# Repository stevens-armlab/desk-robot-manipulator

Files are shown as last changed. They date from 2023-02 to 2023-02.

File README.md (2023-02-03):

# desk-robot-manipulator

## Open-Source Desk Robot Manipulator Design Project
This project is designed to cater towards the growing demand of more ubiquitous open-source robotics software and hardware. The files below provide the materials and resources necessary to recreate this desktop serial robot manipulator with a parallel gripper. 

## CAD Files
Included are individual SolidWorks CAD part files and an overall CAD assembly to help for 3D printing and assembling.
* Download documents as *.stl* files to print on any 3D printer
* This robot uses 5 Dynamixel XL430-W250-T servo motors which can be found [here](https://www.robotis.us/dynamixel-xl430-w250-t/)
* Screws can be found through these links below:
  * [6 - 16mm M2.5](https://www.mcmaster.com/screws/system-of-measurement~metric/thread-size~m2-5/metric-alloy-steel-hex-drive-flat-head-screws/length~16-mm/)
  * [4 - 10mm M2.5](https://www.mcmaster.com/screws/system-of-measurement~metric/thread-size~m2-5/metric-alloy-steel-hex-drive-flat-head-screws/length~10-mm/)
  * [8 - 12mm M2.5](https://www.mcmaster.com/screws/system-of-measurement~metric/thread-size~m2-5/metric-alloy-steel-hex-drive-flat-head-screws/length~12-mm/)
  * [12 - 8mm M2](https://www.mcmaster.com/screws/system-of-measurement~metric/metric-alloy-steel-hex-drive-flat-head-screws/thread-size~m2/length~8-mm)

## Arduino Program
This desk robot uses an [Arduino MEGA](https://store-usa.arduino.cc/products/arduino-mega-2560-rev3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), [Dynamixel Motor Shield](https://www.robotis.us/dynamixel-shield/), [SparkFun Serial Basic Communications Chip](https://www.sparkfun.com/products/14050), and the Arduino IDE as the robot's control mechanisms. To make edits to the code and test out additional programs install [Arduino IDE](https://support.arduino.cc/hc/en-us/articles/360019833020-Download-and-install-Arduino-IDE) and download the DynamixelShield Arduino library [here](https://github.com/ROBOTIS-GIT/DynamixelShield). These will allow you to program using Dynamixel software and upload code to the manipulator. 

Included in this package is the *move_all_motors.ino* Arduino program which takes in input keys *a, w, s, d, j, i, k, l* to control the position of each individual Dynamixel servo. T

Specifications:
* XL430 Dynamixel Servo Motor can be found [here](https://emanual.robotis.com/docs/en/dxl/x/xl430-w250/)
* Dynamixel Motor Shield can be found [here](https://emanual.robotis.com/docs/en/parts/interface/dynamixel_shield/)

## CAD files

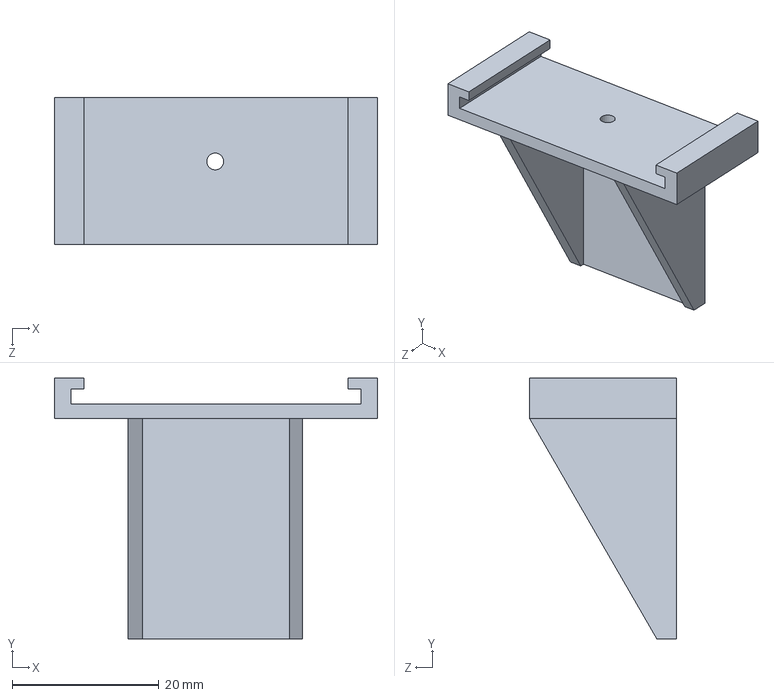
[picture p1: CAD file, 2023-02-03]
CAD Models/robothon_parallelgripper_hand_v4_other_side.SLDPRT
44.0 x 35.5 x 20.0 mm

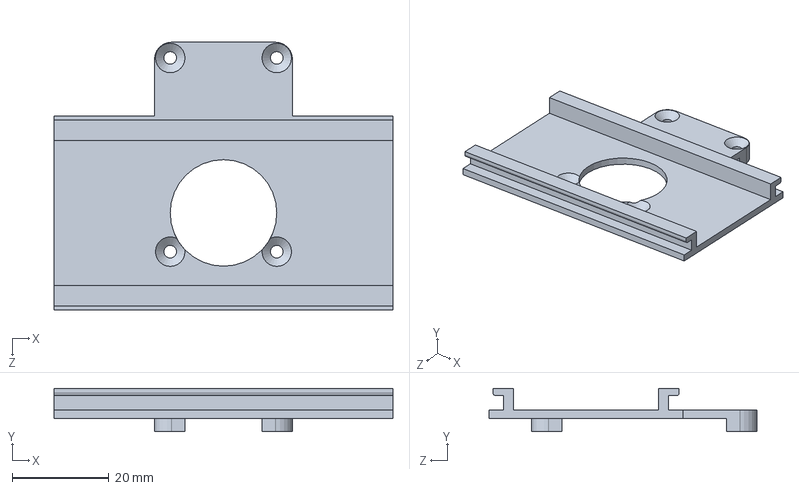
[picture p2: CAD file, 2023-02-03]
CAD Models/robothon_parallelgripper_plate_v4.SLDPRT
70.0 x 8.95 x 55.2 mm

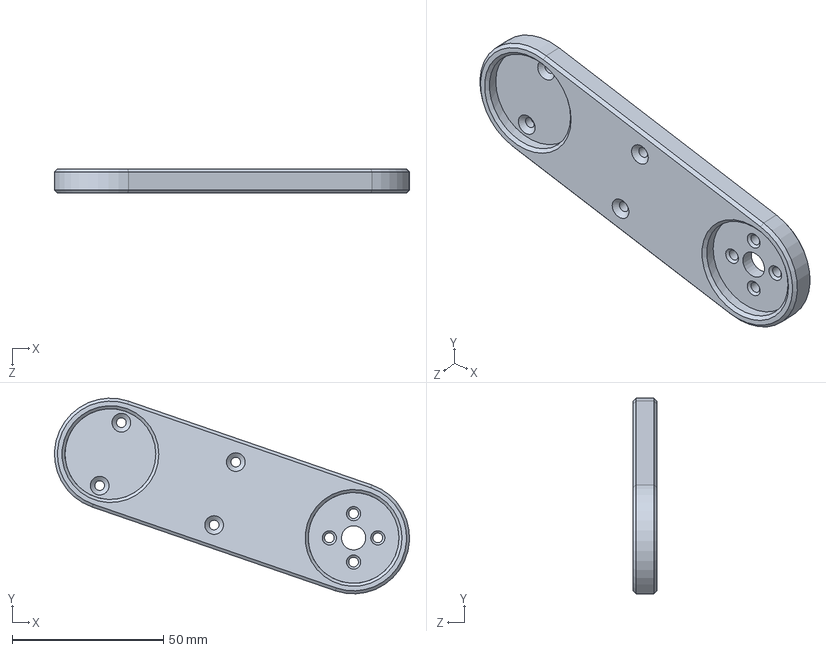
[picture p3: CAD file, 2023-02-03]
CAD Models/Joint 2.SLDPRT
117.3 x 64.7 x 8.00 mm

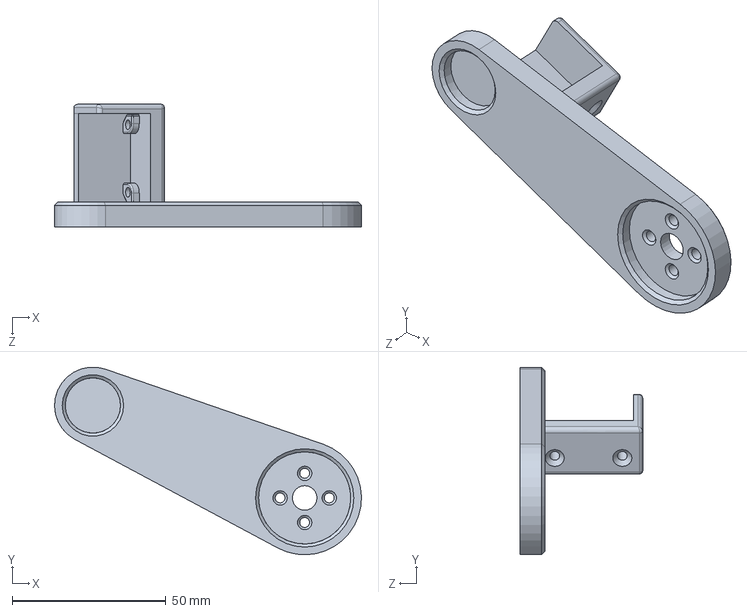
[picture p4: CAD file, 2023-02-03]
CAD Models/Joint 3.SLDPRT
100.0 x 61.0 x 39.9 mm

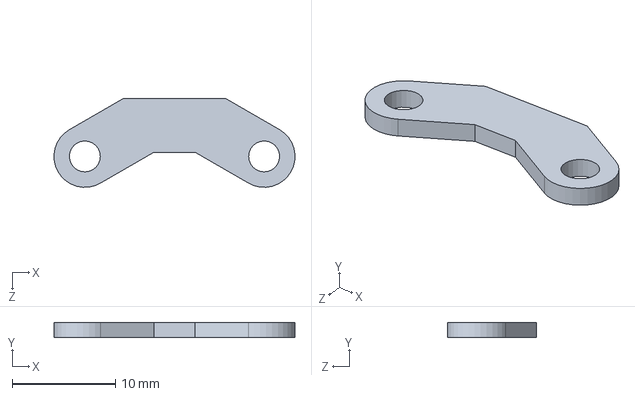
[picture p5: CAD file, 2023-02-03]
CAD Models/robothon_parallelgripper_link_v1.SLDPRT
23.4 x 1.50 x 8.59 mm

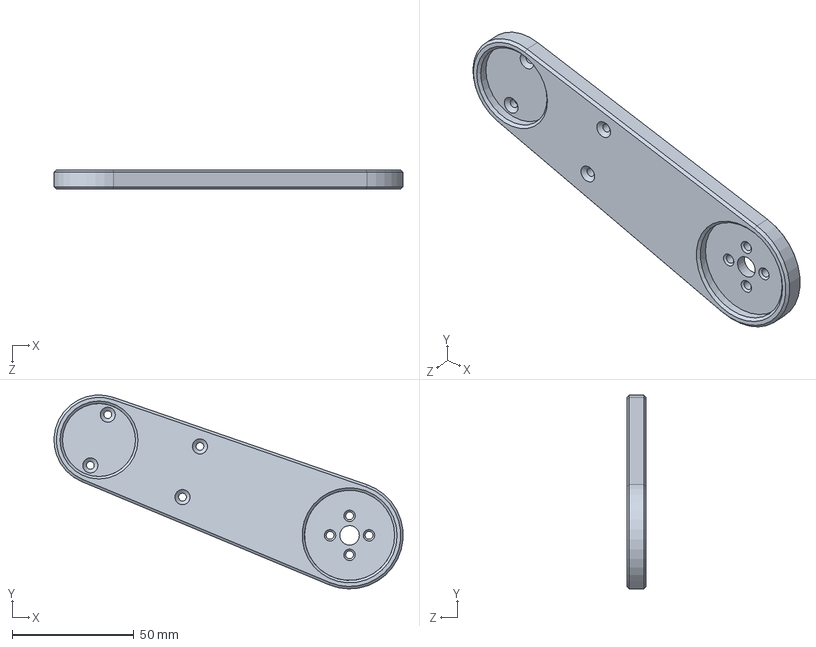
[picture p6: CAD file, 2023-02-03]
CAD Models/Joint 1.SLDPRT
143.3 x 79.6 x 8.00 mm

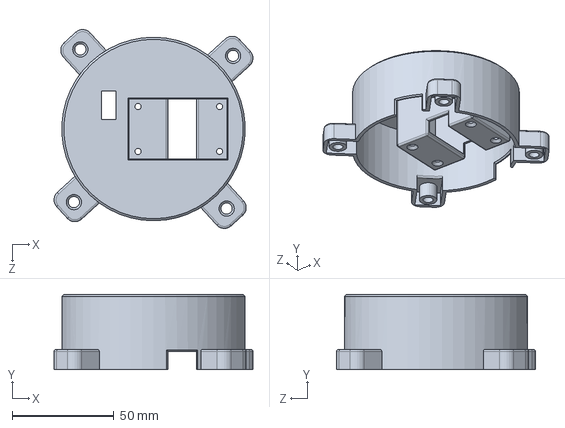
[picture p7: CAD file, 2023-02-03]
CAD Models/Manipulator Base.SLDPRT
97.6 x 37.0 x 97.6 mm

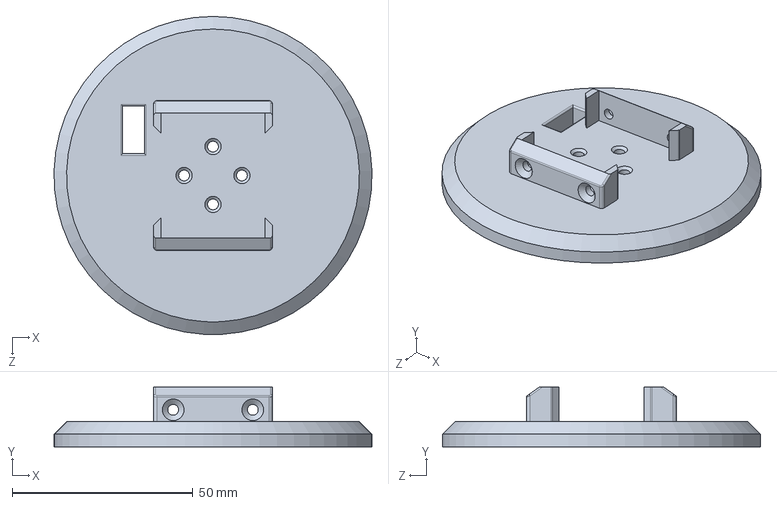
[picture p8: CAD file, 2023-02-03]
CAD Models/Rotator.SLDPRT
88.0 x 16.5 x 88.0 mm

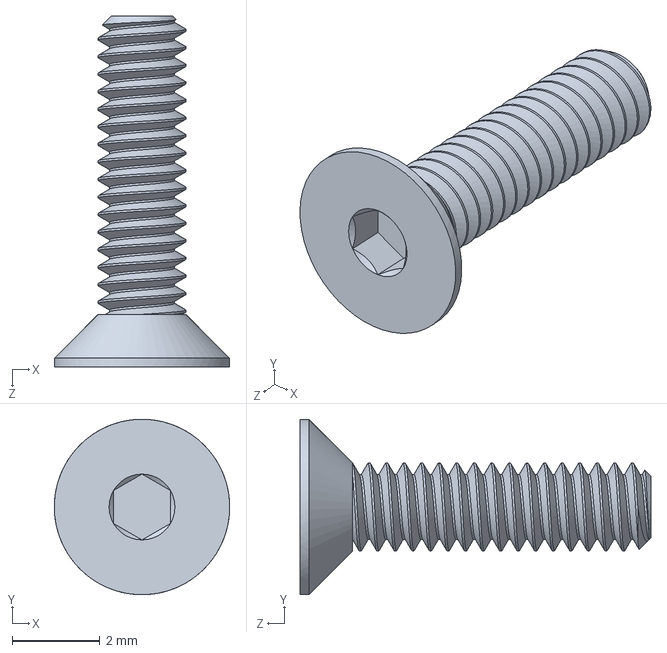
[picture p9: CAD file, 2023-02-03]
CAD Models/Screw-8mm M2.SLDPRT
4.00 x 4.00 x 8.00 mm

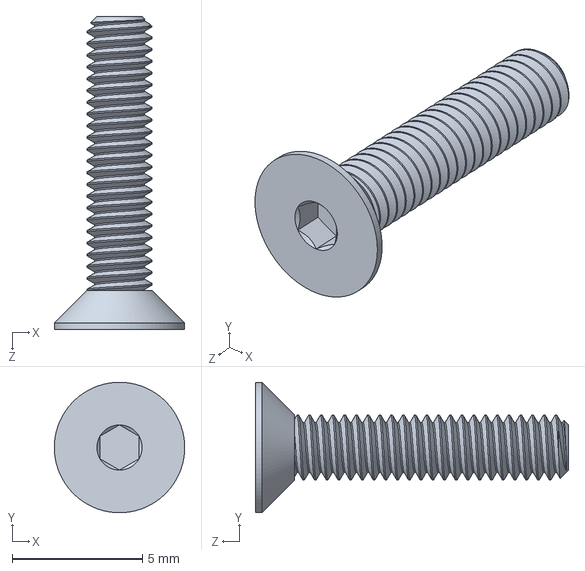
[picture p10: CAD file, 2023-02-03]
CAD Models/Screw-12mm M2.5.SLDPRT
5.00 x 5.00 x 12.0 mm

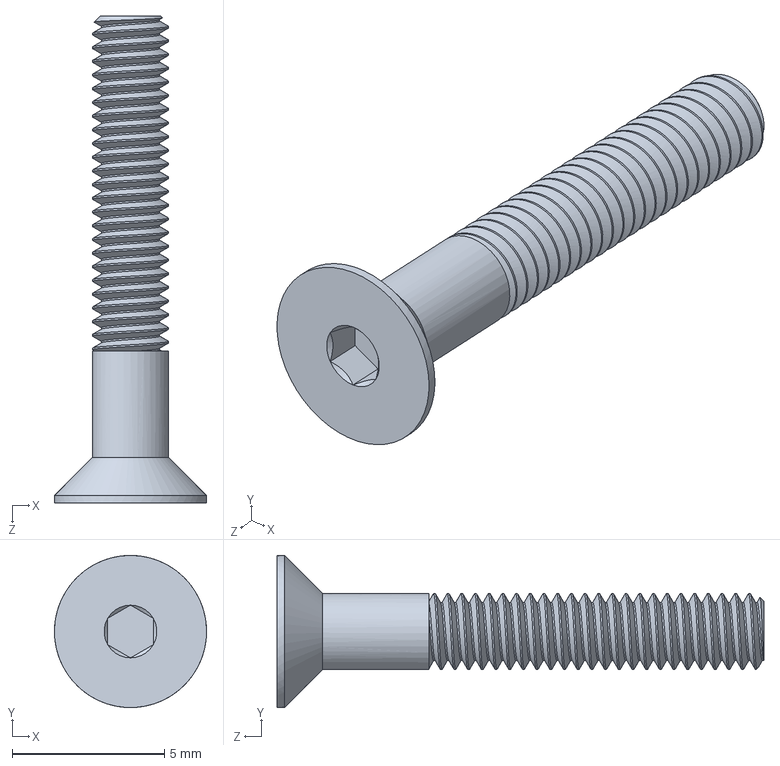
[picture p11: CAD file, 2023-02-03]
CAD Models/Screw-16mm M2.5.SLDPRT
5.00 x 5.00 x 16.0 mm

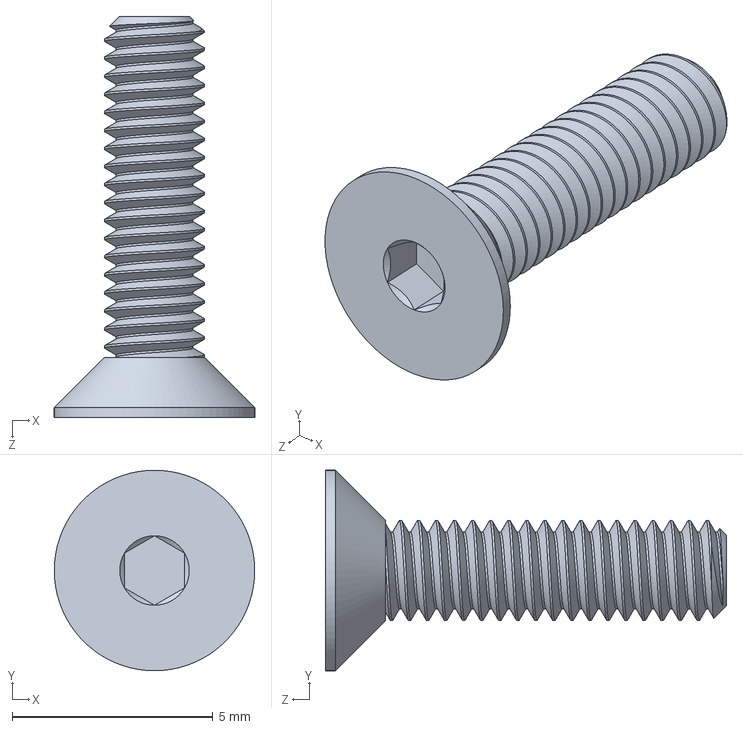
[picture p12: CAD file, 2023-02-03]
CAD Models/Screw-10mm M2.5.SLDPRT
5.00 x 5.00 x 10.0 mm

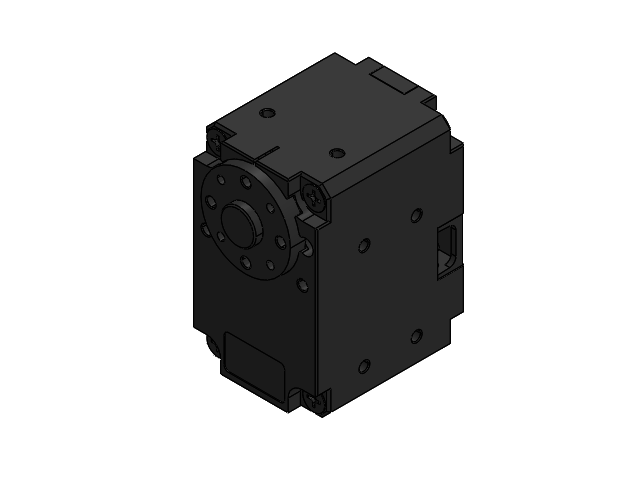
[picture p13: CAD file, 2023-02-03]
CAD Models/XL-430_new.SLDASM
DC11_A01_DUMMY.stp
DX124_SCREW-COVER.stp
B3B-EH.stp x 2
DC11_A01_CASE_CVR_DUMMY.stp
FHS_M2_5X10.stp x 8

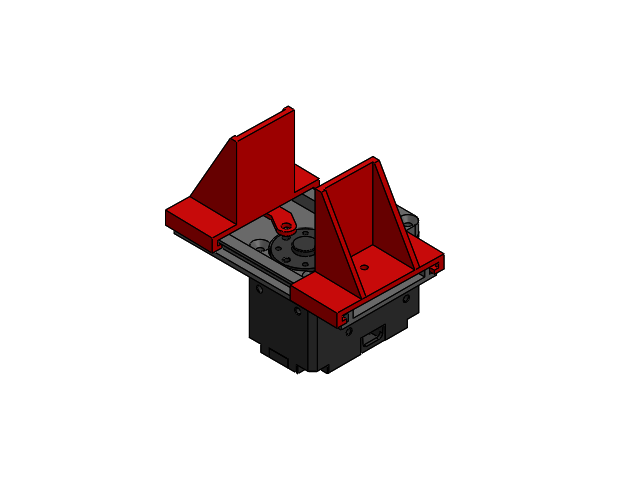
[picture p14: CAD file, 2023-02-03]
CAD Models/Parallel Gripper.SLDASM
robothon_parallelgripper_link_v1 x 2
DC11_A01_DUMMY.stp
DX124_SCREW-COVER.stp
B3B-EH.stp x 2
DC11_A01_CASE_CVR_DUMMY.stp
FHS_M2_5X10.stp x 8
robothon_parallelgripper_hand_v4_other_side
robothon_parallelgripper_plate_v4
robothon_parallelgripper_hand_v4

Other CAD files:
CAD Models/Dynamixel XL430 Motor.SLDASM
CAD Models/robothon_parallelgripper_hand_v4.SLDPRT

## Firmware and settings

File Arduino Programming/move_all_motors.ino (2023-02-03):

#include <DynamixelShield.h>
// ************************ Motor Settings and Variables ******************************* //
#define DEBUG_SERIAL Serial1
const uint8_t DXL_ID_1 = 101;
const uint8_t DXL_ID_2 = 102;
const uint8_t DXL_ID_3 = 103;
const uint8_t DXL_ID_4 = 104;
const uint8_t DXL_ID_5 = 105;
const uint8_t DXL_ID_all[5] = {DXL_ID_1, DXL_ID_2, DXL_ID_3, DXL_ID_4, DXL_ID_5};
const float DXL_PROTOCOL_VERSION = 2.0;
const int32_t BAUD_RATE_MOTOR = 1000000;
DynamixelShield dxl;
char input;
boolean newData = false;

void motor_setup() {
  DEBUG_SERIAL.begin(115200);
  dxl.begin(BAUD_RATE_MOTOR);
  // Set Port Protocol Version. This has to match with DYNAMIXEL protocol version.
  dxl.setPortProtocolVersion(DXL_PROTOCOL_VERSION);
  DEBUG_SERIAL.println("getting dynamixel info");
  for (int i = 0; i<5; i++) {
    // Get DYNAMIXEL information
    dxl.ping(DXL_ID_all[i]);
    // Turn off torque when configuring items in EEPROM area
    dxl.torqueOff(DXL_ID_all[i]);
    dxl.setOperatingMode(DXL_ID_all[i], OP_POSITION);
    dxl.torqueOn(DXL_ID_all[i]);
  }
}

void readSerial() {
  if(DEBUG_SERIAL.available() > 0){
    input = DEBUG_SERIAL.read();
    newData = true;
  }
}

void setup() {
  motor_setup();
  DEBUG_SERIAL.println("void setup");
}

//define function to decrease individual motor position
void moveDecrease(int motorID, char key) {
  int initialPosition = dxl.getPresentPosition(motorID);
  int finalPosition = dxl.getPresentPosition(motorID);
  int i = 15;

  //print out data
  DEBUG_SERIAL.print("Input: ");
  DEBUG_SERIAL.println(key);
  DEBUG_SERIAL.print("Decreasing: ");
  DEBUG_SERIAL.println(motorID);

  //subtracts an increased amount if DYNAMIXEL motor cannot supply enough power initally
  while (initialPosition == finalPosition){
    dxl.setGoalPosition(motorID, dxl.getPresentPosition(motorID) - i);
    finalPosition = dxl.getPresentPosition(motorID);
    i = i - 50;
  }
  DEBUG_SERIAL.println(dxl.getPresentPosition(motorID));
  newData = false;
}

//define function to increase individual motor position
void moveIncrease(int motorID, char key) {
  int initialPosition = dxl.getPresentPosition(motorID);
  int finalPosition = dxl.getPresentPosition(motorID);
  int i = 15;

  //print out data
  DEBUG_SERIAL.print("Input: ");
  DEBUG_SERIAL.println(key);
  DEBUG_SERIAL.print("Increasing: ");
  DEBUG_SERIAL.println(motorID);
  
  //adds additional position increases if DYNAMIXEL motor cannot supply enough power initally
  while (initialPosition == finalPosition){
    dxl.setGoalPosition(motorID, dxl.getPresentPosition(motorID) - i);
    finalPosition = dxl.getPresentPosition(motorID);
    i = i + 50;
  }
  DEBUG_SERIAL.println(dxl.getPresentPosition(motorID));
  newData = false;
}


void loop() {
  // readSerial function uses Serial input to run the following switch case
  readSerial();
  if(newData == true){
    //case inputs can be changed to any key
    switch(input){
      // Motor 1 controlling manipulator base
      case ' ':
        moveIncrease(DXL_ID_1, ' ');
        break;
      case '.':
        moveDecrease(DXL_ID_1, '.');
        break;
        
      // Motor 2 controlling joint 1
      case 'a':
        moveIncrease(DXL_ID_2, 'a');
        break;
      case 'd':
        moveDecrease(DXL_ID_2, 'd');
        break;
        
      // Motor 3 controlling joint 2
      case 'w':
        moveDecrease(DXL_ID_3, 'w');
        break;
      case 's':
        moveIncrease(DXL_ID_3, 's');
        break;
        
      // Motor 4 controlling joint 3
      case 'j':
        moveIncrease(DXL_ID_4, 'j');
        break;
      case 'l':
        moveDecrease(DXL_ID_4, 'l');
        break;
        
      // Motor 5 controlling gripper 
      case 'i':
        moveIncrease(DXL_ID_5, 'i');
        break;
      case 'k':
        moveDecrease(DXL_ID_5, 'k');
        break;
        
      // Enter any other key to stop the motors
      default:
        newData = false;
        break;
    }
  }
}
